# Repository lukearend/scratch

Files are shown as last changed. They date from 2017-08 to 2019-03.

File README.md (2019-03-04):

# scratch
_an open-source, autonomously-balancing mobile robot built from scratch_

See it in action [here](https://youtu.be/LrDqXtu8--8)!

## Overview

*scratch* is a self-balancing mobile robotics platform. The robot balances itself on two wheels using IMU sensors and a feedback loop with its motors. It drives using commands dictated from the user via a Sony DualShock 3 gamepad controller. Its balancing functions are handled by an Arduino Mega microcontroller, and its higher-level driving instructions and operations are handled by an on-board Raspberry Pi communicating with the Arduino. The goal of the project is to implement hierarchical control structure and explore the development of complex behavior in a partially autonomous mobile robotics system.

## How it works

### Goal of the self-balancing robot

The task at hand is to create a mobile robot which balances itself on two wheels. This is an implementation of the *inverted pendulum*, a classical problem in dynamics and control theory. The premise is simple: there is a pendulum which has its center of mass above its pivot point. This is an unstable equilibrium point, so in practice it will fall over due to noise in the environment. The goal is to move the pivot point horizontally in such a way that the weight remains upright. Naturally, this model and its variants are also important in the field of robotics and have seen several applications in recent years.

In the case of the self-balancing robot, the task is to drive the two wheels such that the agent maintains an upright, balanced posture. In theory, the problem is fairly straightforward. The agent must first acquire some knowledge of its current position in respect to its desired position. Next, it must calculate the actions needed to achieve its desired position. Finally, it needs to adjust its motor outputs accordingly in order to carry out these actions despite various affecting factors in the environment. This is carried out via a *closed-loop control system*, where actual sensory feedback is integrated with the desired state of the system in order to adjust the system toward its desired state.

In practice a solution is somewhat complicated. The real world poses a suite of complicating factors including sensor noise, computation time, and mechanical slippage. The implications of some of these factors are considered in the section below, where a practical solution to the self-balancing robot is briefly explained.

### Using accelerometer and gyroscope for angle estimate

It is essential that the agent has an awareness of its own position. In the case of the self-balancing robot, this means that the agent must know the angle of its body with respect to vertical at any given point.

To this end, two sensors are applied - the accelerometer and the gyroscope. The accelerometer measures the component of acceleration being experienced along any of the three axes at any given time. When the accelerometer is in a steady state, the primary acceleration experienced is that due to gravity. This essentially allows the accelerometer to tell which way is "down." In our case, the x and z components of the accelerometer are given to be in the plane of the robot as it tips forward and backwards. Thus, given both of these sensor readings, we can use inverse tangent trigonometry to calculate an angle estimate of the body from the accelerometer.

The gyroscope gives relatively low-noise readings, but accumulates bias over time; the accelerometer is very noisy but unbiased. The two sensors are integrated via a Kalman filter to provide a state estimate.

### Lowest level PID loop for motors
A very low-level short-time scale PID controller for each wheel adjusts the raw voltage supplied to the motor in order to achieve a target wheel speed.

### Middle level balancing PID loop
A mid-level PID controller adjusts the motor speed to supply to the low-level PID controller in order to orient the body to a particular target angle.

### Highest level driving PID loop, driving control and filtering
A high-level, longer-time scale PID controller adjusts the target angle to shoot for in order to achieve a target velocity.

The target velocity is given by the user via Playstation controller, and this signal can also be used to bias the robot toward balancing in one location.

### Peripherals such as proximity sensors (with filters) and servo motor neck
The robot is outfitted with a number of proximity sensors which could be used in the future for autonomous navigation. It also has a servo motor neck which points in the direction it is driving. This could be outfitted with a Raspberry Pi camera to do something like optic flow analysis for visual feedback or simple facial recognition using a lightweight convolutional neural network.

### Serial communication
The Arduino and Raspberry PI communicate asynochronously over serial. The Arduino control loop operates on a much faster timestep than the Raspberry Pi, so the Arduino receives a driving command every few loops. The Raspberry Pi waits, every loop, to hear back from the Arduino.

### Raspberry Pi connecting to controller using sixad and pairing with sixpair
The Raspberry Pi must be paired with the Playstation controller using sixad and pairing with sixpair. See [this blog](http://booting-rpi.blogspot.com/2012/08/dualshock-3-and-raspberry-pi.html) for a walkthrough.

## Instructions

### Starting up from completely powered down

#### Visual assessment

1. Visually assess the robot and its connections. Are the batteries charged? Are both battery packs plugged in properly (including the Turnigy lithium-polymer battery being plugged into the low voltage alarm)? Is the serial communication line between the Raspberry Pi and the Arduino intact? Are the servo motors hooked up properly? Are all the screw terminals holding securely? Having any wires become unseated from the protoboards? Are there any loose or fraying wires?

#### Launching the Raspberry Pi

2. Switch on the Raspberry Pi power bank. This can be done by pressing the power button found on the left, outer-facing side of the robot.

3. Gain access to the Raspberry Pi. The Raspberry Pi is running headlessly (which means it is not connected to any monitor, keyboard, mouse, etc.), so it must be controlled somehow. This can be done by hooking up an HDMI monitor and USB keyboard/mouse, or by accessing its command line through a remote secure shell server (enter `ssh pi@192.168.194.240` (or the Pi’s IP address) or `mosh pi@192.168.194.240` (if using the mosh client) into a terminal session connected over the same network, and enter the password, raspberry, when prompted, to connect). *(See appendix 3 for list of useful Linux shell commands).*

4. Launch the script. From the Raspberry Pi shell, enter the command `sudo python3 Programming/Python/Programs/flexibot.py` to launch the program which connects to the Sony DualShock 3 gamepad controller and operates the balancing robot.

5. The program will go through its initialization process. Follow the printed prompts to connect to the controller via Bluetooth. It may take several tries to get the Raspberry Pi to recognize the controller. *If this step is repeatedly unsuccessful, see appendix 4 for troubleshooting).*

6. Once the controller is connected, the Raspberry Pi will open its serial port and begin its communications with the Arduino.

7. At this point, the Raspberry Pi no longer needs to be controlled directly by the user. The monitor, keyboard, and/or mouse can be unplugged or the ssh or mosh session can be terminated. The Pi is now up and ready to go!

#### Launching the Arduino

8. Hold the robot in a straight upright position. This will help it get started off on the right foot, so to speak.

9. Throw the metal toggle switch on the front of the robot from `OFF` to `ON`.

10. The robot will calibrate and initialize itself, which should only take a second or so. The robot will then begin to balance on its own. *(If it does not spring into action at this point, see appendix 4 for troubleshooting).*

11. The system is now entirely operational.

### Operation instructions

#### Using the controller

Now that the robot is up and running, it can be operated by the user with the Sony DualShock 3 gamepad controller:

<table>
  <tr>
    <td>Left joystick left/right (mode 1)</td>
    <td>Turn left/right</td>
  </tr>
  <tr>
    <td>Right joystick up/down (mode 1)</td>
    <td>Drive forwards/backwards</td>
  </tr>
  <tr>
    <td>Left joystick up/down (mode 2)</td>
    <td>Left wheel forwards/backwards</td>
  </tr>
  <tr>
    <td>Right joystick up/down (mode 2)</td>
    <td>Right wheel forwards/backwards</td>
  </tr>
  <tr>
    <td>Left bumper</td>
    <td>Toggle between mode 1 and mode 2</td>
  </tr>
  <tr>
    <td>Right bumper</td>
    <td>Invert controls (aircraft style)</td>
  </tr>
  <tr>
    <td>D-pad up/down</td>
    <td>Increase/decrease speed multiplier by .25 m/s (min 0, default .5, max 1)</td>
  </tr>
  <tr>
    <td>D-pad right/left (!)</td>
    <td>Increase/decrease drive smoothing factor by .1 (min 0, default 1, max 1)</td>
  </tr>
  <tr>
    <td>Start (!)</td>
    <td>Launch/terminate autonomous mode</td>
  </tr>
  <tr>
    <td>Select (!)</td>
    <td>Terminate script</td>
  </tr>
</table>

The controls marked with the *(!)* sign are advanced controls. These should be operated with discretion, by the experienced user:

* It is recommended that maximum drive smoothing is used all the time, for the most stable and safe driving.

* Autonomous mode is highly experimental and subject to potentially destructive failures. It is worth mentioning that any movement of the joysticks at all during autonomous mode will manually override, terminating autonomous mode and giving control back to the user instantly.

* Terminating the script will require regaining access to the Raspberry Pi if the user wishes to relaunch the program.

Finally, pressing down all four buttons (triangle, circle, cross, and square) at the same time momentarily will reboot the Raspberry Pi (note that this does not relaunch the script). Holding these down for 3 seconds will cause the Raspberry Pi to shut down and remain powered off.

#### Driving tips

* When in doubt, go slow. There is generally more stability at slower speeds, and less stability at high speeds.

* Be very cautious when negotiating rough or uneven terrain. This is especially true where there are small gaps or elevated lips on the floor changing from one type of surface to another. If negotiated improperly, these can easily cause the robot to tip over violently. It is best to attempt to drive over these slowly and evenly. It is essential to cross at a 45 degree angle rather than head on so that the obstacle is handled one wheel at a time.

* The robot should be able to handle disturbances such as pushes or kicks to the top fairly well, but there is a limit. Pushing the robot’s wheels or holding them in place will likely cause it to fall over. The mobility of the wheels is the only mechanism by which it is able to balance itself.

* Do not pick up the robot while it is balancing. This disrupts the feedback loop in the robot’s control structure.

* Do not drive the robot into walls, or obstacles that will not allow its wheels to rotate.

* Do not operate on wet, slippery, sandy, or fiery surfaces.

### Powering down

The Arduino and Raspberry Pi have been designed to be capable of operating independently of one another. In other words, the Arduino can be switched on and off (for instance to drive the robot, pick it up and carry it for a while, drive it again) while the Raspberry Pi script is still running and staying connected to the controller. Likewise, the Arduino can operate independently of the Raspberry Pi, in which case the robot will simply balance in place devoid of driving instructions. The two should be able to switch on and off independently of one another.

When the user wishes to completely shut down the system, the following steps should be followed:

1. Switch off the Arduino. Make sure that it is held or properly supported so that it does not fall over.

2. Shut down the Raspberry Pi. This can be done by holding down all four buttons on the controller (triangle, circle, cross, and square) at the same time for three seconds. Otherwise, (such as if the controller has become disconnected, or the program was terminated), it can be done by plugging in a keyboard (or accessing via a remote shell server client) and issuing the shell command `sudo shutdown -h now`. This tells the Raspberry Pi to shut down immediately, and stay powered down (this is called a system halt). The yellow LED activity light on the Raspberry Pi will blink 10 times when it has fully shut down.

* *Important note:** It is absolutely imperative that the Raspberry Pi is properly shut down before its power supply is removed! Improper shutdown or simply switching off its power supply/pulling the plug can corrupt its filesystem, with the possibility of irreparably damaging the SD card and losing everything.

3. It is now safe to switch off the Raspberry Pi’s power bank. Hold the power button on the left outward-facing side of the robot for approximately one second until the power bank’s blue LED bars stop glowing.

4. The system is now entirely shut down.

### Battery management and storage

One crucial element to the long-term use and operation of the robot is proper management of the batteries powering the various devices making up the system.

#### Sony DualShock 3 gamepad controller battery

The controller operates wirelessly, so it must be recharged on occasion. Typically, a full charge will last for hours of use and takes only about 20-30 minutes. To charge, simply use a USB 2.0 A-male to mini-B cable to plug the controller into the Raspberry Pi when it is powered on. Note: the controller can be charged by plugging into some other devices, but this will cause it to become unpaired with the Raspberry Pi. It will have to be physically re-paired again with the Raspberry Pi after charging on another device.

#### Raspberry Pi power bank

Make sure that the Raspberry Pi is properly shut down before turning off the power bank and removing the USB power connection between the bank and the Raspberry Pi. The power bank can be recharged by plugging into a USB port or USB wall adapter with a USB 2.0 A-male to micro-B cable. The bank does not support through-charging, so it cannot be both charged and used to power the Raspberry Pi at the same time. The blinking blue LED bars on the side of the bank indicate its level while charging; when all the bars are on and no longer blinking, the bank is full.

#### Turnigy lithium-polymer battery

First of all, lithium-polymer batteries are volatile and highly dangerous if used improperly. It is strongly recommended that the user educate themselves on proper care, use, and storage of these batteries before operating the robot in any way.

The low voltage alarm will indicate when the battery needs to be recharged. Do not continue to operate the robot once the alarm has indicated that the cells are reaching low voltages, or else the battery may be irreparably damaged. 

To recharge the battery, the user should first completely shut down the robot. Then the battery can be carefully unplugged from the robot and removed from the chassis.  The battery should be charged using a proper lithium-polymer balance charger. Lithium-polymer batteries should never be charged unsupervised because of the risk of fire or explosion. Once the battery is charged, it can be once again carefully plugged back into the robot. Remember to plug it into the low voltage alarm as well, ensuring that it is connected with the proper polarity.

#### Storage

There are a few things to consider when storing the robot inactively for extended periods of time. 

First of all, the Raspberry Pi should be properly shut down and the Raspberry Pi power bank should be completely turned off.

Next, the battery should be unplugged from the low voltage alarm. If it remains plugged in, the alarm (which has several LEDs) will continue to sap power from the battery until it is completely dead. If a lithium-polymer battery is drained completely, it becomes irreparably damaged and is effectively rendered worthless. It is thus essential that the battery does not remain plugged into the low voltage alarm if it is not being used in the near future.

Furthermore, lithium-polymer batteries should not be stored for long periods of time at full charge or at low charge, or else the health of the battery will be adversely affected. Thus, the battery must be stored at a partial charge. This can be done by choosing the "STORAGE" setting on the balance charger, which will bring the cells to a proper voltage for safe and healthy long-term storage.

## Current known issues

*Serial communications breakdown may occur between the Arduino and the Raspberry Pi.* They are communicating at very high baud rates with very rapid control loops.

*The WiFi module on the Raspberry Pi sometimes does not work properly, and the Raspberry Pi can have issues connecting to the internet even with a wired internet connection.* This may be due to the Bethel ITS department’s current work on restructuring the network.

*The robot may struggle to balance on rough terrain or when encountering large disturbances.* Continuing work is being done on optimizing the balancing control algorithms.

*The servo motor head will sometimes become unresponsive while the rest of the robot continues to work properly.* This rare issue is likely caused by some sort of communication disruption between the Arduino and the ServoShield.

*Autonomous mode is still in the earliest stages of development.* The robot does not yet demonstrate advanced or even particularly successful autonomous behavior over extended periods of time.

## Future improvements

### Hardware

A small LCD touch screen will be mounted to the servo neck of the robot, as well as a PiCamera to be operated by the Raspberry Pi script. 3D print designs for these mounting cases have already been designed. The screen could be used to operate the Raspberry Pi easily, or display some type of robotic face or video stream. The camera could be used to capture images and video and save them to the Raspberry Pi’s filesystem. It also opens up the possibility for types of object recognition or machine vision to be incorporated in the future.

### Software

Now that a solid hardware robotics platform has been developed for the most part, the main future developments will be on the software side. The goal is to pursue deeper levels of autonomy in the form of hierarchical control structure, developing more advanced behaviors and combinations of reflex arcs. Measures may be taken to model functions of the human central nervous system in developing an efficient and effective control structure. Hopefully this system can be used as a platform to study real-world implementations of reinforcement learning, statistical learning, pattern recognition, localization and mapping, and other types of machine learning and artificial intelligence.

## Parts list

### Frame/Chassis

* M3 frame bolt *(numerous)*

* M3 nut *(numerous)*

* aluminum M3 L-bracket connector piece *(numerous)*

* aluminum M3 45-degree connector piece *(numerous)*

* aluminum M3 right angle connector piece *(numerous)*

* 4.0 cm aluminum frame piece *(x4)*

* 6.0 cm aluminum frame piece *(x5)*

* 10.0 cm aluminum frame piece *(x4)*

* 15.0 cm aluminum frame piece *(x6)*

* 20.0 cm aluminum frame piece *(x2)*

* [Actobotics 1.50" aluminum channel](https://www.sparkfun.com/products/12383)

  -fits perfectly around Turnigy lipo battery to hold it in using friction

* bottom chassis plate (with mounting holes for motors)

* neck chassis plate (with mounting holes for servo motor neck)

* 3M double-sided foam adhesive tape

* foam padding

* toggling power switch for Arduino power supply

* mounting board for Raspberry Pi (Sketchup files included)

* mounting board for Arduino

* mounting board for power regulator

* 4-40 standoff bolt (plastic) *(numerous)*

* 4-40 nut (plastic) *(numerous)*

* 4-40 washer (plastic) *(numerous)*

### Power supply

* [Turnigy 2200 mAh 3s 20C lithium-polymer battery pack](http://www.google.com/url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)

  -power supply for Arduino, its peripherals, DC motors and all lower-level sensors

* [AmazonBasics 5600 mAh portable power bank](http://www.amazon.com/AmazonBasics-Portable-Power-Micro-Cable/dp/B00LRK8HJ8)

  -power supply for Raspberry Pi and its peripherals

* [HobbyKing lipoly low voltage alarm](http://www.hobbyking.com/hobbyking/store/__18987__On_Board_Lipoly_Low_Voltage_Alarm_2s_4s_.html)

  -connected to lipo battery, alerts user when battery reaches low voltages

* [Polulu step-down voltage regulator D15V70F5S3](https://www.pololu.com/product/2111)

  -takes 11.1V from lipo battery and drops it to 5V to power Arduino and its sensors

### Arduino

* Arduino Mega 2560

  -the central microprocessing unit of the balancing sensors and control structure

* [Sparkfun MegaShield kit](https://www.sparkfun.com/products/9346)

  -prototyping shield for Arduino Mega

* [Sparkfun 3.3-5V bi-direction logic level converter](https://www.sparkfun.com/products/12009)

  -for interfacing Arduino serial communication (operating at 5V) with Raspberry Pi GPIO serial communication (operating at 3.3V)

* [Mini modular breadboard](https://www.sparkfun.com/products/12043) *(x2)*

  -adhesively attached to MegaShield for prototyping on the Mega

### DC motor control

* [Polulu dual MC33926 motor drive shield for Arduino](https://www.pololu.com/product/2503)

  -contains H-bridge circuitry to operate the DC motors to provide balancing functions

  -capable of operating at relatively high currents without heating up significantly

  -no heatsink needed

* Brushed DC motor with optical encoder *(x2)*

* [BaneBots 4 7/8 robot wheel](http://banebots.com/pc/WHB-WS-498/T80P-494BO-U3) *(x2)*

### Sensors

* [Sparkfun 9DOF LSM9DS0 IMU breakout](https://www.sparkfun.com/products/12636)

  -combined accelerometer/gyroscope/magnetometer sensor used for calculating an estimated angle of the robot, configured to communicate with Arduino via I2C protocol

  -*important:* operates at 3.3V

* [Sparkfun 3.3-5V bi-direction logic level converter](https://www.sparkfun.com/products/12009)

  -for interfacing Arduino I2C (operating at 5V) with LSM9DS0 I2C (operating at 3.3V)

* [Sharp GP2Y0A41SK0F short range infrared proximity sensor](https://www.sparkfun.com/products/12728) *(x4)*

  -two placed on front of robot facing forwards, two placed on back of robot facing backwards

  -used to help robot detect objects in autonomous exploration mode

* [Infrared sensor jumper wire](https://www.sparkfun.com/products/8733) *(x4)*

* [Mini modular breadboard](https://www.sparkfun.com/products/12043) *(x2)*

  -prototyping space where IMU sensor and its level shifter are wired

  -adhesively attached to back of battery mount, centered directly on axis with the wheelbase between DC motors

### Servo motor control

* [Renbotics ServoShield V2.0](http://www.seeedstudio.com/depot/Renbotics-ServoShield-V20-p-1299.html)

  -configured to communicate with Arduino via I2C in order to control up to 16 servos

  -*important:* the printed labels on the hardware channels 1-16 actually correspond to software channels 0-15; this discrepancy is handled in the Arduino program

* Servo motor *(x2)*

  -these servos provide 2 degrees of freedom for the neck: tilting forwards to backwards, and swiveling left to right

* Servo neck mounting pieces

### Raspberry Pi

* [Raspberry Pi 2 Model B](https://www.raspberrypi.org/products/raspberry-pi-2-model-b/)

  -the central high-level control unit taking wireless commands from controller via Bluetooth, and communicating them to Arduino via serial on GPIO pins

* [SanDisk Ultra 16GB microSDHC Class 10 memory card](http://www.bestbuy.com/site/sandisk-ultra-16gb-microsdhc-class-10-memory-card-black/4120107.p?id=1218457270079)

  -memory card housing filesystem for Raspberry Pi

* [Bluetoth 4.0 USB module](https://www.adafruit.com/products/1327)

  -provides Bluetooth capabilities for wireless communication with Sony DualShock 3 gamepad controller

* [Miniature WiFi (802.11b/g/n) module](https://www.adafruit.com/products/814)

  -provides WiFi capabilities to Raspberry Pi

  -especially useful for setting up remote SSH server (this [mosh mobile shell client](https://mosh.mit.edu/) is highly recommended) in order to remotely access Raspberry Pi command shell

  -also useful for setting up a remote VNC server (this [RealVNC remote VNC viewer](https://www.realvnc.com/) is highly recommended) in order to remotely access Raspberry Pi X-server desktop (the graphic user interface launched via "startx" command)

  -these features offer fantastically flexible operation of the Raspberry Pi; it can be controlled headlessly and wirelessly in the robot without the need to physically plug in a keyboard, mouse and monitor every time the user must execute a command, launch a script, properly shut down, etc.

* [Sony DualShock3 wireless gamepad controller](http://www.amazon.com/PlayStation-Dualshock-Wireless-Controller-Black-3/dp/B0015AARJI)

  -operated by user to drive the robot

  -communicates wirelessly with Raspberry Pi via Bluetooth

### Essential development tools and peripheral devices

* [IMAX B6 Lipro digital balance charger](http://www.amazon.com/Original-Lipro-Digital-Balance-Charger/dp/B006TT49O4)

  -used to charge/balance/store/discharge lithium-polymer batteries

* operating system running Arduino IDE environment

  -for developing and uploading Arduino source code to robot (written in Arduino C/C++)

* USB 2.0 A-male to B-male cable

  -for connecting Arduino to computer for uploading source code and serial monitoring

* HDMI-capable external monitor

  -for graphic display of Raspberry Pi during development

* USB keyboard

  -for keyboard control of Raspberry Pi during development

* USB mouse

  -for mouse control of Raspberry Pi during development

* USB 2.0 A-male to mini-B cable

  -for connecting Sony DualShock 3 gamepad controller to Raspberry Pi for charging and initial pairing process

* USB hub

  -allows several USB peripherals to connect to Raspberry Pi over one USB port

## Wiring connections and pinout

### Wiring diagram

*(See appendix 1.1.)*

### Pinout list

#### Arduino pinout

<table>
  <tr>
    <td>Analog input 0</td>
    <td>Motor L current sensing</td>
  </tr>
  <tr>
    <td>Analog input 1</td>
    <td>Motor R current sensing</td>
  </tr>
  <tr>
    <td>Analog input 4</td>
    <td>Front-left proximity sensor reading</td>
  </tr>
  <tr>
    <td>Analog input 5</td>
    <td>Front-right proximity sensor reading</td>
  </tr>
  <tr>
    <td>Analog input 6</td>
    <td>Back-left proximity sensor reading</td>
  </tr>
  <tr>
    <td>Analog input 7</td>
    <td>Back-right proximity sensor reading</td>
  </tr>
  <tr>
    <td>Digital 4</td>
    <td>Motor shield enable pin</td>
  </tr>
  <tr>
    <td>Digital 7</td>
    <td>Motor L direction pin</td>
  </tr>
  <tr>
    <td>Digital 8</td>
    <td>Motor R direction pin</td>
  </tr>
  <tr>
    <td>Digital 9</td>
    <td>Motor L pulse width modulation pin</td>
  </tr>
  <tr>
    <td>Digital 10</td>
    <td>Motor R pulse width modulation pin</td>
  </tr>
  <tr>
    <td>Digital 12</td>
    <td>Motor fault flag pin</td>
  </tr>
  <tr>
    <td>Digital 14 (Tx3)</td>
    <td>Serial communication with Raspberry Pi (Tx)</td>
  </tr>
  <tr>
    <td>Digital 15 (Rx3)</td>
    <td>Serial communication with Raspberry Pi (Rx)</td>
  </tr>
  <tr>
    <td>Digital 16</td>
    <td>Encoder L direction reading</td>
  </tr>
  <tr>
    <td>Digital 17</td>
    <td>Encoder R direction reading</td>
  </tr>
  <tr>
    <td>Digital 18 (interrupt 5)</td>
    <td>Encoder L interrupt pin</td>
  </tr>
  <tr>
    <td>Digital 19 (interrupt 4)</td>
    <td>Encoder R interrupt pin</td>
  </tr>
  <tr>
    <td>Digital 20 (SDA)</td>
    <td>Data signal for I2C communication</td>
  </tr>
  <tr>
    <td>Digital 21 (SCL)</td>
    <td>Clock signal for I2C communication</td>
  </tr>
</table>

#### ServoShield pinout

<table>
  <tr>
    <td>Hardware pin 15/Software pin 14</td>
    <td>Neck tilting servo motor</td>
  </tr>
  <tr>
    <td>Hardware pin 16/Software pin 15</td>
    <td>Neck swiveling servo motor</td>
  </tr>
</table>

#### Raspberry Pi pinout

<table>
  <tr>
    <td>Pin #6/GND</td>
    <td>Serial communication with Arduino (ground)</td>
  </tr>
  <tr>
    <td>Pin #8/GPIO14 (TxD0)</td>
    <td>Serial communication with Arduino (Tx)</td>
  </tr>
  <tr>
    <td>Pin #10/GPIO15 (RxD0)</td>
    <td>Serial communication with Arduino (Rx)</td>
  </tr>
</table>

### Device connection diagram

*(See appendix 1.2.)*

## Appendices

### 1.1 Wiring diagram

This diagram shows the electrical circuit connections of the entire system.

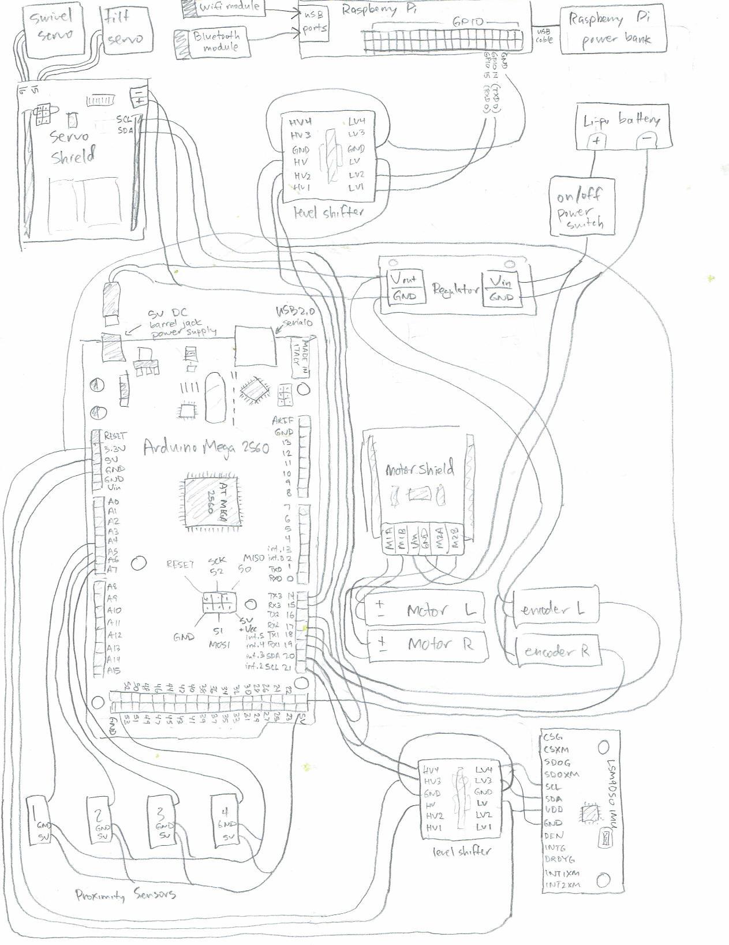
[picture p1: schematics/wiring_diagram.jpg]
wiring diagram


### 1.2 Device connection diagram

This diagram shows the overall connections between the various devices in the system. The hope is to give a general overview of which components are connected to each other, and how they are working together.

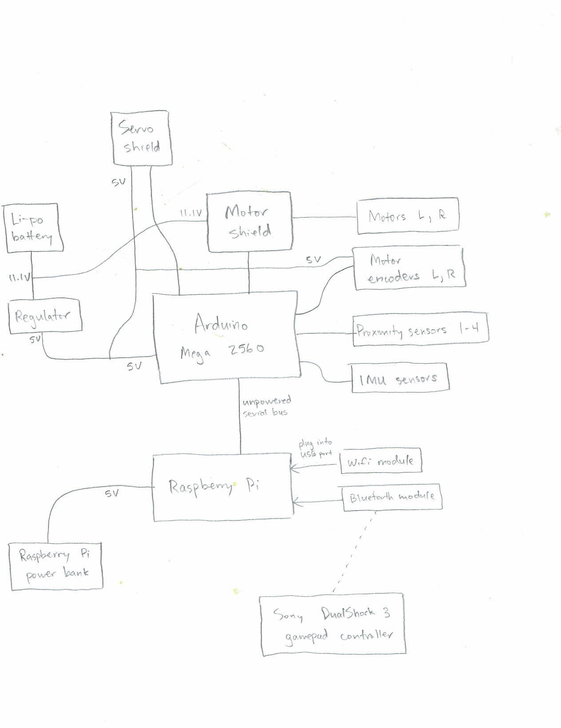
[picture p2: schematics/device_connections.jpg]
device connections


### 2.1 Hierarchical PID structure

This diagram shows the hierarchical nature of the primary PID controllers used in the system--a technique known as cascading PID control. The design of this system is modeled after the human central nervous system, where the brain influences the activity of the spinal cord to command voluntary movements. This is done through a hierarchy of control levels: *strategy* (represented by the association areas of neocortex and basal ganglia of the forebrain), *tactics* (represented by the motor cortex and cerebellum), and *execution* (represented by the brain stem and spinal cord).

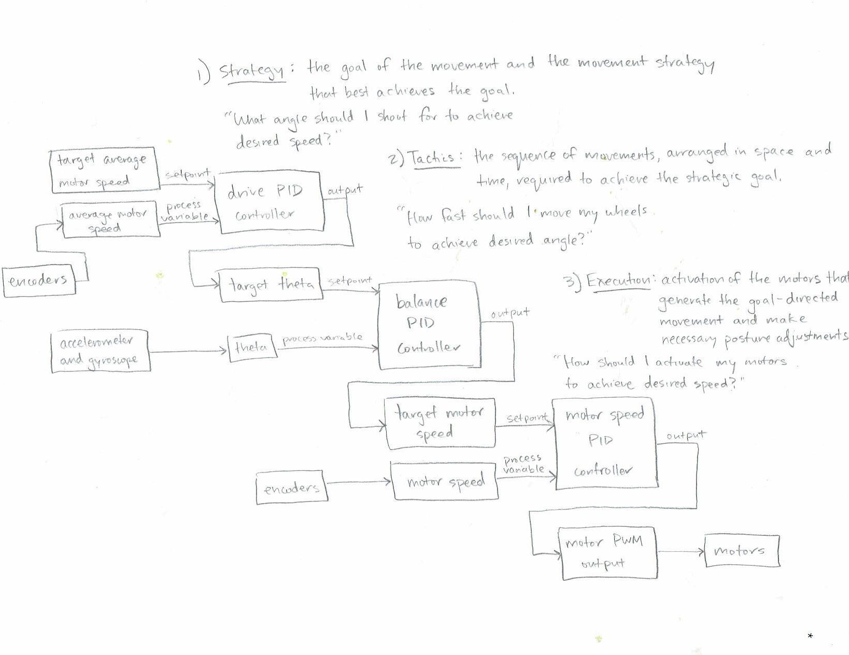
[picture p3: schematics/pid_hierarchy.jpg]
PID hierarchy


### 2.2 Control process block diagram

This diagram shows the flow of all control process occurring simultaneously in the robot.

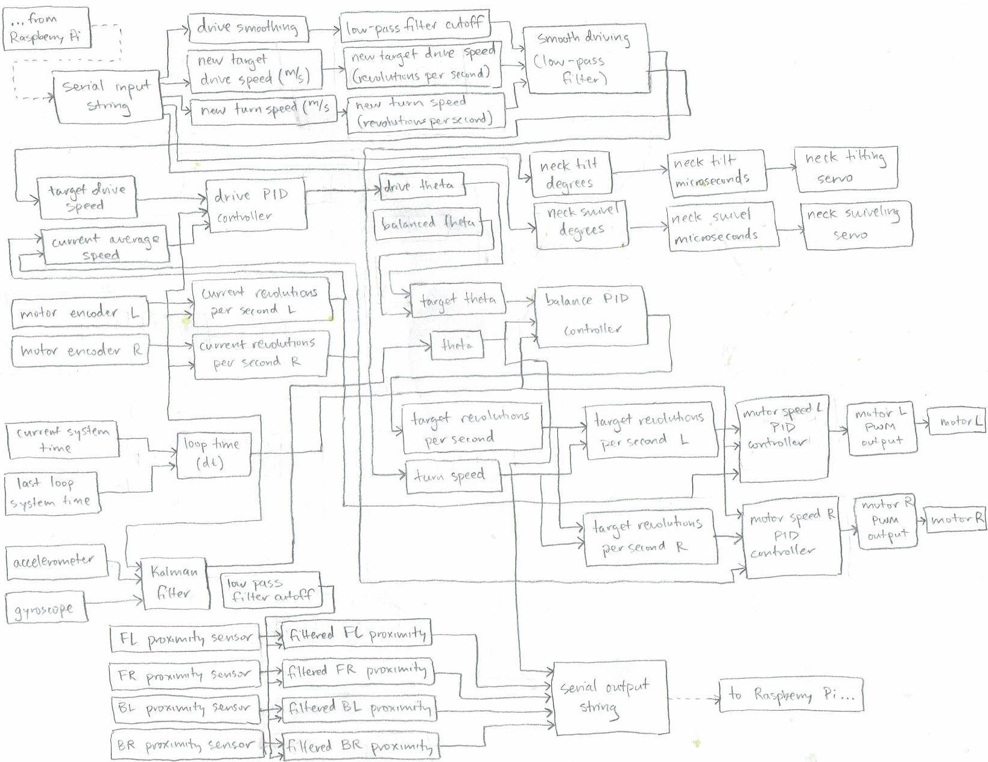
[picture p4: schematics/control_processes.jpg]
control processes


### 3. Useful Linux shell commands

`startx`: used to launch the graphic user interface (starts the X server which is the desktop)

`cd`: ‘call directory,’ navigates to the home directory

`cd ..`: navigates to the parent directory (up one folder)

`ls`: ‘library show,’ shows the contents of the current directory

`rm`: ‘remove,’ used to remove a file or directory

`sudo`: ‘superuser do,’ a powerful prefix that carries out any following command with superuser privileges (used when a command is being denied due to lack of permissions)

`sudo apt-get update`: connects to the internet and automatically downloads the latest updates for the distribution, should be run periodically and before major installments

`sudo service bluetooth status`: returns the current status of Bluetooth

`hciconfig`: displays useful information regarding Bluetooth functionality

`sudo ./sixpair`: runs an executable file pairing the Sony DualShock 3 gamepad controller with the Raspberry Pi (essentially performs a handshake with the controller)

`ifconfig`: displays useful information regarding network connection and various network devices such as ethernet and WiFi chips; can be used to find out current IP address

`sudo nano /etc/network/interfaces`: allows user to access and edit a text file containing important network configuration options; this is the file that must be used to set up a static IP address

`sudo reboot`: immediately reboots the Raspberry Pi

`sudo shutdown -h now`: immediately shuts down the Raspberry Pi and enters system halt mode where the filesystem is unmounted and the Raspberry Pi will stay powered down; it is then safe to unplug power supply

### 4. Troubleshooting

#### Raspberry Pi issues

*The Raspberry Pi boots up to a black screen.*

Check that the Raspberry Pi power bank is fully charged (all four blue LED bars are lit). Sometimes the Raspberry Pi needs to be operating on a fully charged battery to supply the power needed to launch the graphic user interface. Once the Pi is up and running, however, the power bank can generally run down without issue.

*The Linux shell is giving the error message *command not recognized* (or some similar variant).*

Check that the command is typed out exactly properly, letter for letter. Make sure that the user is currently in the correct folder, if attempting to carry out a particular command or access a particular file. See appendix for a list of useful Linux shell commands.

*The Python script repeatedly fails to connect to the Sony DualShock 3 gamepad controller.*

This could happen for a variety of reasons:

-Check that the Sony DualShock 3 gamepad controller is charged and working. The four red LED lights on the front should flash on and off when the PlayStation button is pressed.

-Try powering the controller off and back on again. Hold down the PlayStation button for approximately 10 seconds to shut off the controller, then try connecting again.

-Make sure that the Bluetooth chip is working properly. Enter the shell command sudo service bluetooth status and the response should be bluetooth is enabled. if Bluetooth is working correctly.

-If these are not the issue, the controller may need to be physically re-paired with the Raspberry Pi. This is the case if the controller has been plugged into another computer for charging, or has been used on another device. Follow these instructions in the Linux shell:

Enter the command cd in order to navigate to the home directory.

Enter the command cd Programming to navigate to the directory called "Programming". This directory contains an executable file called “sixpair”.

Plug the controller into the Raspberry Pi using a USB 2.0 A-male to mini-B cable.

Run the command sudo ./sixpair in order to pair the two devices. If they have paired successfully, the output should look similar to this:

Current Bluetooth master: DE:AD:BE:EF:00:00

Setting master bd_addr to**: 00:1F:81:00:06:2**

Now that the devices have been paired, the controller can be unplugged from the Raspberry Pi.

Navigate back to the home directory with the command cd and execute the script sudo python3 Programming/Python/Programs/flexibot.py again in order to re-attempt connecting the controller wirelessly.

-If these measures are unsuccessful, try following the instructions found in [this guide](http://booting-rpi.blogspot.com/2012/08/dualshock-3-and-raspberry-pi.html).

*The robot is up and balancing, but the Sony DualShock 3 gamepad controller does nothing.*

This means that the Arduino is working properly in balancing the robot, but it is not receiving driving commands from the Raspberry Pi. This could be because the Raspberry Pi has stopped running its script, or the script is still running and the controller is not being detected by the Raspberry Pi. Try re-starting the script.

In any case, the Arduino is programmed to simply stop and balance in place in the absence of driving commands from the Raspberry Pi. *Informational note:* in qualitative experiments, the Bluetooth communication between the controller and the robot demonstrated an impressive range. It is likely that the robot would drive out of sight before its connection to the controller would be dropped.

#### Arduino issues

*When switching on the Arduino, the red power LED turns on but the robot does not start balancing.*

This issue is suspected to occur occasionally when the Arduino’s Serial3 buffer has been filled up by data streaming from the Raspberry Pi. This prevents the Arduino from going through its normal initialization process and launching its code, springing into action. Try switching off the Arduino, carefully unplugging the ribbon cable serial connection to the Raspberry Pi, and firmly plugging it back in again. Try switching on the Arduino again.

*The robot sort of balances, but it begins to drive itself in circles and falls over.*

This nasty issue occurs when the motor encoder on one of the wheels is not providing proper feedback. Try carefully observing the electrical activity on pins 16-19 with an oscilloscope while manually rotating the wheels to check if everything is working properly. The line in the Arduino source code responsible for driving the motors normally must be commented out in order to try this.

#### Hardware issues

*The robot is balancing somewhat well, but one of the wheels is a little bit jerky; almost as if it is lagging behind the other wheel.*

Switch off the robot and check that both wheels are tightened into the axle properly. If a wheel has become loose, it must be removed off and the axle must be tightened with a small hex key.

## Acknowledgments

Thanks to Profs. Nathan Lindquist and Adam Johnson at Bethel University for their mentorship and guidance throughout this project.

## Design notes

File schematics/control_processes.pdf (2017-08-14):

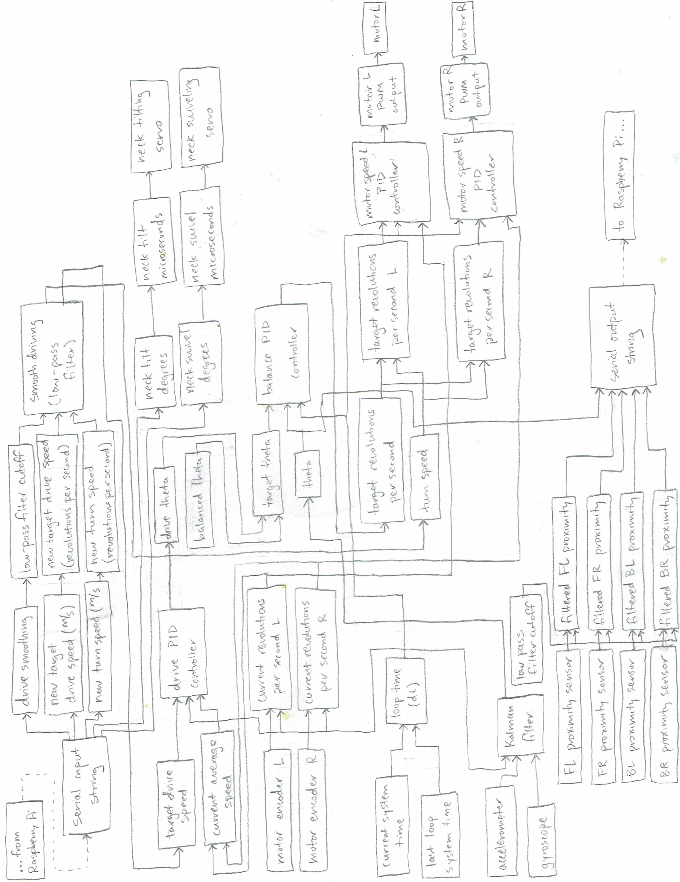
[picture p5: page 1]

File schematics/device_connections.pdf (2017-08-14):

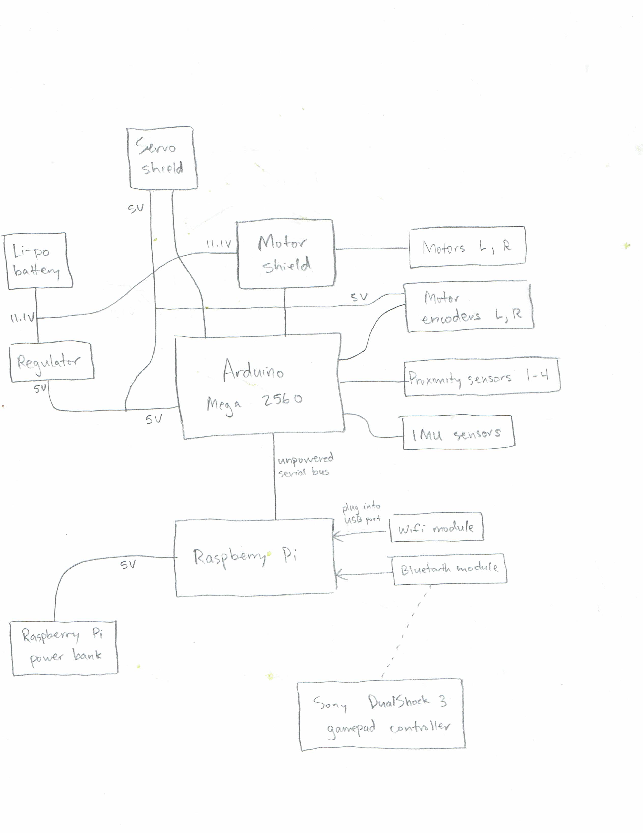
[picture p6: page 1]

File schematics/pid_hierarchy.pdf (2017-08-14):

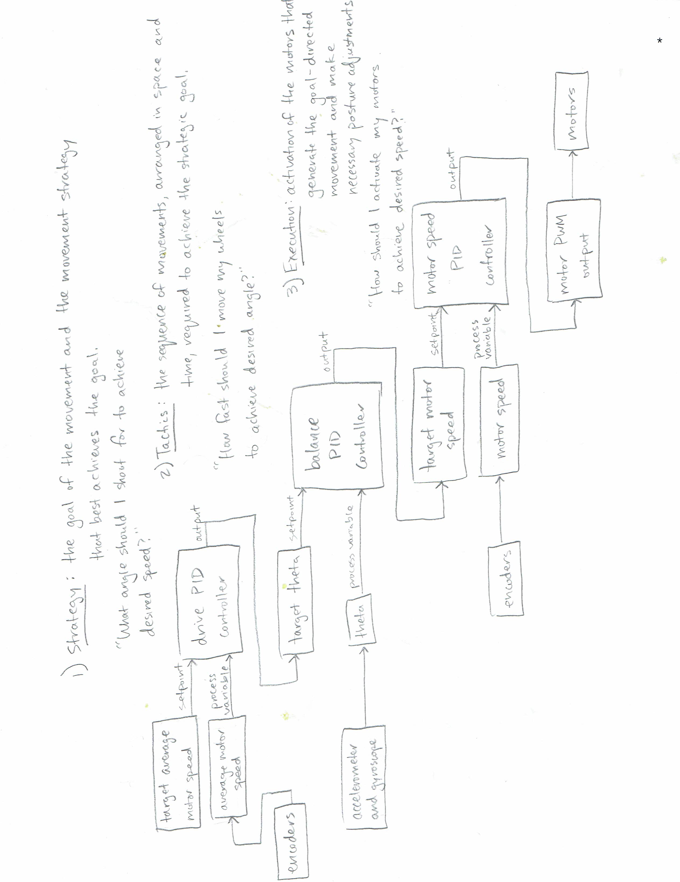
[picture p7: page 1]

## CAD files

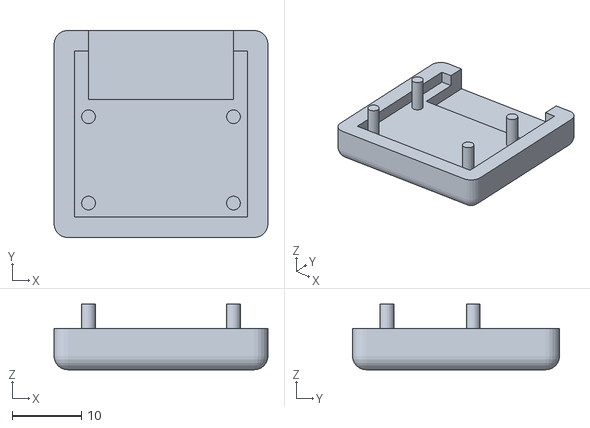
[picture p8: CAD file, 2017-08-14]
3d_prints/picamera_case/piCameraCaseBottom.stl
31.0 x 30.0 x 9.50

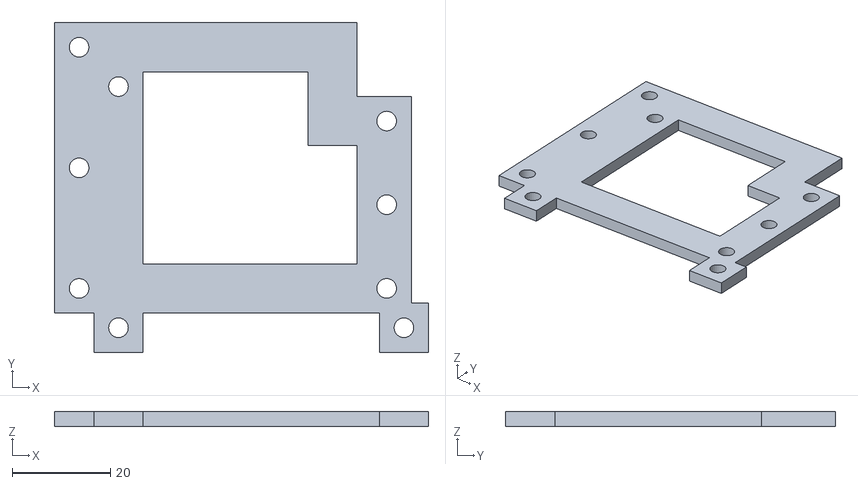
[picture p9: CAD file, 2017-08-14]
3d_prints/rpi_mount/raspberryPiMount.stl
76.0 x 67.0 x 3.00

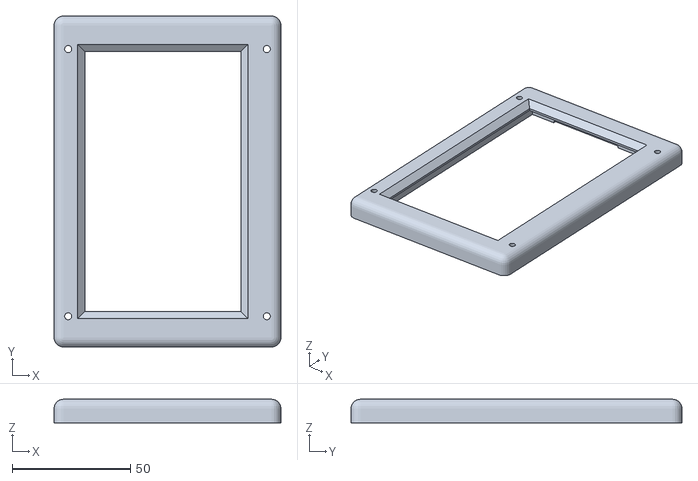
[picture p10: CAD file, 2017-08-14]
3d_prints/touchscreen_case/touchscreenCaseTop.stl
96.0 x 140.0 x 10.0

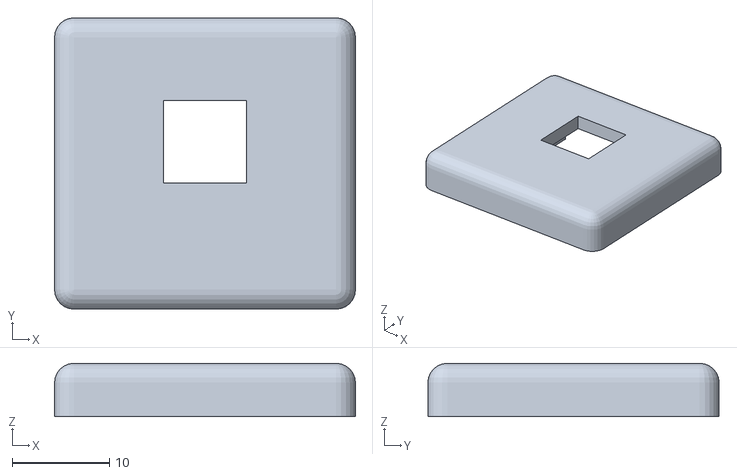
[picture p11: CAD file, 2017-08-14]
3d_prints/picamera_case/piCameraCaseTop.stl
31.0 x 30.0 x 5.50

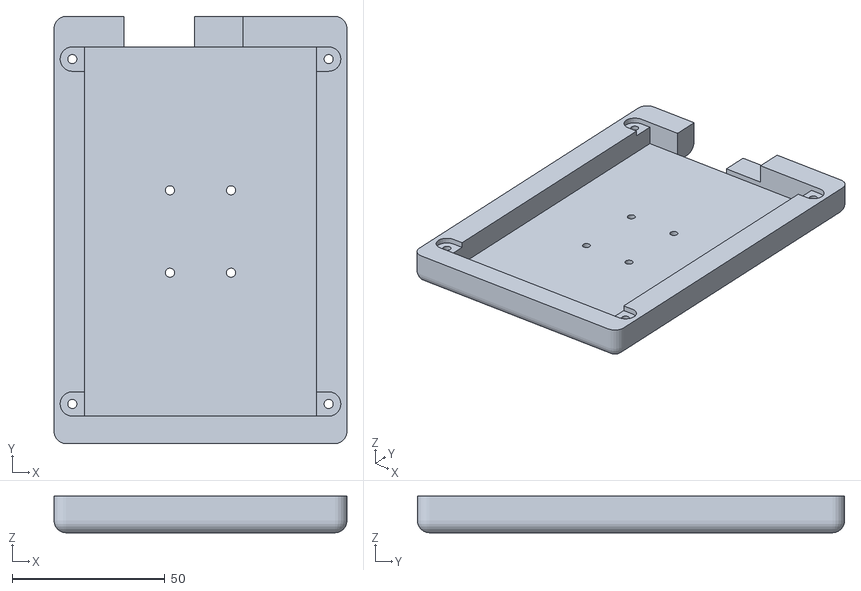
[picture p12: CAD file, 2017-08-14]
3d_prints/touchscreen_case/touchscreenCaseBottom.stl
96.0 x 140.0 x 12.0

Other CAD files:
3d_prints/picamera_case/piCameraCase.skp
3d_prints/rpi_mount/raspberryPiMount.skp
3d_prints/touchscreen_case/touchscreenCase.skp

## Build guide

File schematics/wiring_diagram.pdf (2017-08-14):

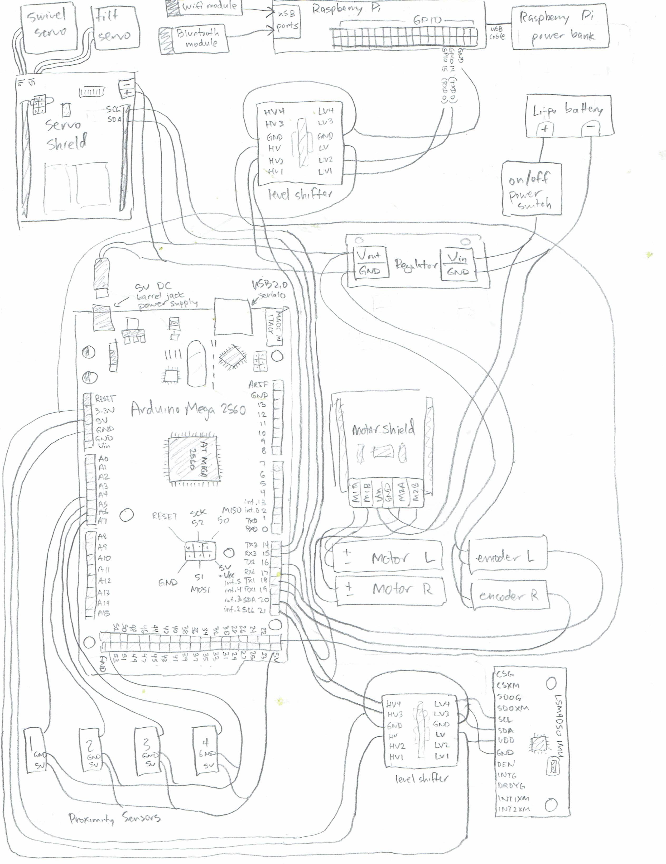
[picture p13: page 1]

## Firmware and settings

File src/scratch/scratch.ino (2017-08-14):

//////////////////////////////////////////////////////////////
//////////////////////////////////////////////////////////////
//////////////////////////////////////////////////////////////
//////////////////////////////////////////////////////////////
//////////                                          //////////
//////////                                          //////////
//////////                 SCRATCH                  //////////
//////////          for Arduino Mega 2560           //////////
//////////               Version 1.0                //////////
//////////                                          //////////
//////////                Luke Arend                //////////
//////////                Summer 2015               //////////
//////////        Bethel University NanoLab         //////////
//////////                                          //////////
//////////    Copyright © 2015 Bethel University    //////////
//////////           All rights reserved.           //////////
//////////                                          //////////
//////////                                          //////////
//////////////////////////////////////////////////////////////
//////////////////////////////////////////////////////////////
//////////////////////////////////////////////////////////////
//////////////////////////////////////////////////////////////




/*  PROJECT NOTES
 *  Enjoy!
 *  
 *  Hardware notes:
 *  -Wheel circumference is .388 m
 *  -Encoders will register 3000 counts per revolution
 *  -The left motor encoder sometimes has issues.
 *  -The left wheel sometimes physically becomes loose on the axle.
 *  -Make sure the motor shield is able to draw enough current--should not be an issue.
 *  -Arduino serial port 1 is open for communication with user via USB cable.
 *  -Arduino serial port 3 is connected via a 5v-3.3v level shifter to a Raspberry Pi.
 *  -The IMU sensors are read over I2C protocol.
 *  -The four infrared proximity sensors are read via an ADC over I2C protocol.
 *  -The angle positions for the servo motors in the neck correspond to microseconds in
 *  the PWM duty cycle. By experimentation, the following mapping was foundg:
 *    DEGREES <---->  MICROSECONDS
 *    TILT SERVO:
 *    0       <---->  1060
 *    45      <---->  1320
 *    90      <---->  1580
 *    135     <---->  1840
 *    <<180   <---->  1960
 *    SWIVEL SERVO:
 *    >>0     <---->  1000
 *    45      <---->  1220
 *    90      <---->  1500
 *    135     <---->  1780
 *    <<180   <---->  2000
 *  
 *  Software notes:
 *  -PID controllers are used throughout. I highly recommend the Ziegler-Nichols PID tuning method
 *  as a starting point.
 *  -I tend to err on the side of clarity at the expense of brevity. I often employ long or even
 *  descriptive function and variable names, or even ever-so-slightly suboptimal code for the sake
 *  of spelling out what is really going on.
 *  -There is heavy use of global variables. When programming for embedded microcontrollers this is 
 *  something of a necessary evil, and many of the pitfalls that normally accompany globals do not 
 *  apply. In this case, it often makes things simpler and allows more flexibility with functions. 
 *  The extensive use of global variables is a conscientious decision that I stand by.
 *  -I changed the Adafruit_ADS1015 library in order to optimize the proximity sensor reading speeds.
 *  Because of this, the pin mapping for the ADC converter is somewhat different because each is
 *  actually reading the sensor at the pin called before it. To read a physical pin, follow this mapping:
 *    read hardware pin 0 -> call software pin 0x01
 *    read hardware pin 1 -> call software pin 0x02
 *    read hardware pin 2 -> call software pin 0x03
 *    read hardware pin 3 -> call software pin 0x00
 *  -Due to this hangup, for the time being we are using analog read pins for the proximity sensors.
 */




//////// Library includes ////////
#include <math.h> // yay! we can do ALL the trigs
#include <SPI.h>  // included for SPI communications
#include <Wire.h> // included for I2C communications
#include <Adafruit_ADS1015.h> // library for using the ADS1015 12-bit ADC (optimized to be faster)
#include <SFE_LSM9DS0.h>  // library for using the LSM9DS0 9DOF gyro/accel/mag IMU
#include <ServoShield2.h>  // for neck servo motors



//////// Constant definitions ////////
//// Constants for motor encoders ////
#define ENCODER_L_BITMASK 2 // bit mask for a low level readng of pin 16
//^ ATmega2560 pin 13, PH1 ( TXD2 ), (port H, address B00000010)
#define ENCODER_R_BITMASK 1 // bit mask for a low level reading of pin 17
//^ ATmega2560 pin 12, PH0 ( RXD2 ), (port H, address B00000001)


//// Constants for driving control ////
#define RPS_TO_MPS .388 // constant conversion rate for revolutions per second to meters per second
#define MPS_TO_RPS 2.57732  // constant conversion rate for meters per second to revolutions per second


//// Tuning constants for drive PID controller ////
#define DRIVE_OUTPUT_GAIN 1 // output gain used to scale controller
#define DRIVE_P_GAIN 6.5  // P gain 6.5
#define DRIVE_I_GAIN 5  // I gain 7
#define DRIVE_D_GAIN .045 // D gain .045


//// Constants for IMU sensor ////
// I2C address constants for SFE_LSM9DS0 library //
#define LSM9DS0_XM_ADDR 0x1D // I2C address of accel/mag
#define LSM9DS0_G_ADDR  0x6B // I2C address of gyro

// Constants for scaling sensor readings //
#define RAD_TO_DEG 57.29578 // constant conversion rate for radians to degrees
#define DEG_TO_RAD 0.0174533  // constant conversion rate for degrees to radians
#define ACCEL_SCALE_X -1.09 // used to "zero out" accel readings at 1g
#define ACCEL_OFFSET_X 0
#define ACCEL_SCALE_Z -1.05
#define ACCEL_OFFSET_Z -.05


//// I2C address constant for ADC converter ////
#define ADS1015_ADDR 0x48


//// I2C address constant for servo shield ////
#define SERVO_SHIELD_ADDR 0x7F // can be changed with switch register on servo shield


//// Constants for Kalman filter ////
#define R_MEASUREMENT 0.03  // measurement noise variance (how much you distrust new measurements)
#define Q_ANGLE 0.001 // accelerometer variance (how much you distrust accelerometer readings)
#define Q_GYROBIAS 0.003  // gyro bias variance (how much you distrust gyro readings)
//^ these constants must be estimated or derived experimentally


//// Tuning constants for motor speed PID controller ////
#define SPEED_OUTPUT_GAIN 1 // output gain used to scale controller
#define SPEED_P_GAIN 180 // P gain 180
#define SPEED_I_GAIN 2000.15  // I gain 2000.15
#define SPEED_D_GAIN 1.57639  // D gain 1.57639


//// Tuning constants for balance PID controller
#define BALANCE_OUTPUT_GAIN -1  // output gain used to scale controller
#define BALANCE_P_GAIN 10.8  // P gain 10.8
#define BALANCE_I_GAIN 189.968  // I gain 189.968
#define BALANCE_D_GAIN .002  // D gain .002

#define DEFAULT_BALANCE_THETA 3 // the theta of the robot (with no adjustments) resulting in balance



//////// Class constructors ////////
//// Proximity sensors class ////
Adafruit_ADS1015 adc(ADS1015_ADDR); // class instance for ADS1015 called 'adc'


//// IMU class ////
LSM9DS0 imu(MODE_I2C, LSM9DS0_G_ADDR, LSM9DS0_XM_ADDR); // class instance for LSM9DS0 called 'imu'


//// Servo motor classes ////
ServoShield2 neck = ServoShield2(SERVO_SHIELD_ADDR, 50); // class instance for controlling neck servos
//^ sets servo update rate to 50 Hz mode



//////// Pin assignments ////////
//// Pin assignments for motor encoders ////
const byte encoderLpinA = 18;  // ATmega2560 pin 46, address PD3 (TXD1/INT3)
const byte encoderLpinB = 19;  // ATmega2560 pin 45, address PD2 (RXD1/INT2)
const byte encoderRpinA = 20;  // ATmega2560 pin 44, address PD1 (SDA/INT1)
const byte encoderRpinB = 21;  // ATmega2560 pin 43, address PD0 (SCL/INT0)


//// Pin assignments for infrared proximity sensors ////
/*const byte proxFLpin = 0x01; // front-left proximity sensor ADS1015 pin
const byte proxFRpin = 0x02; // front-right proximity sensor ADS1015 pin
const byte proxBLpin = 0x03; // back-left proximity sensor ADS1015 pin
const byte proxBRpin = 0x00; // back-right proximity sensor ADS1015 pin
//^ refer to project notes for why these are what they are*/

const byte proxFLpin = A4; // front-left proximity sensor ADS1015 pin
const byte proxFRpin = A5; // front-right proximity sensor ADS1015 pin
const byte proxBLpin = A6; // back-left proximity sensor ADS1015 pin
const byte proxBRpin = A7; // back-right proximity sensor ADS1015 pin


//// Pin assignments for motor driver  ////
const byte motorEnablePin = 4; // LOW = disabled, HIGH = enabled, toggling resets latched fault condition
const byte motorFaultPin = 12; // status flag indicator (LOW indicates fault)

const byte motorLpin = 7; // Polulu Dual MC33926 motor driver channel 1 direction input
const byte pwmLpin = 9;  // Polulu Dual MC33926 motor driver channel 1 speed input
const byte motorRpin = 8; // Polulu Dual MC33926 motor driver channel 2 direction input
const byte pwmRpin = 10; // Polulu Dual MC33926 motor driver channel 2 speed input

const byte motorLcurrentPin = A0;
const byte motorRcurrentPin = A1;


//// Pin assignments for servo neck (these pins are on ServoShield) ////
const byte neckTiltPin = 14;
const byte neckSwivelPin = 15;


//// Pin assignments for flexible actuators ////
const byte flex0driveApin = 23;
const byte flex0driveBpin = 25;
const byte flex0enablePin = 22;
const byte flex0currentPin = 62;  // A8
const byte flex1driveApin = 27;
const byte flex1driveBpin = 29;
const byte flex1enablePin = 24;
const byte flex1currentPin = 63;  // A9
const byte flex2driveApin = 31;
const byte flex2driveBpin = 33;
const byte flex2enablePin = 26;
const byte flex2currentPin = 64;  // A10
const byte flex3driveApin = 35;
const byte flex3driveBpin = 37;
const byte flex3enablePin = 28;
const byte flex3currentPin = 65;  // A11
const byte flex4driveApin = 39;
const byte flex4driveBpin = 41;
const byte flex4enablePin = 30;
const byte flex4currentPin = 66;  // A12
const byte flex5driveApin = 43;
const byte flex5driveBpin = 45;
const byte flex5enablePin = 32;
const byte flex5currentPin = 67;  // A13
const byte flex6driveApin = 47;
const byte flex6driveBpin = 49;
const byte flex6enablePin = 34;
const byte flex6currentPin = 68;  // A14
const byte flex7driveApin = 51;
const byte flex7driveBpin = 53;
const byte flex7enablePin = 36;
const byte flex7currentPin = 69;  // A15

const byte flex0num = 0; // gives pins 23, 25, 22, A8 (62)
const byte flex1num = 1; // gives pins 27, 29, 24, A9 (63)
const byte flex2num = 2; // gives pins 31, 33, 26, A10, (64)
const byte flex3num = 3; // gives pins 35, 37, 28, A11 (65)
const byte flex4num = 4; // gives pins 39, 41, 30, A12 (66)
const byte flex5num = 5; // gives pins 43, 45, 32, A13 (67)
const byte flex6num = 6; // gives pins 47, 49, 34, A14 (68)
const byte flex7num = 7; // gives pins 51, 53, 36, A15 (69)
//^ refers to the motor number, from which the pins can be derived as a linear function
//^ this saves from having to type out all the pin numbers when they follow an easy pattern



//////// Global variable declarations ////////
//// Global variables for loop timing ////
long int dt;  // main loop time step in microseconds
long unsigned int lastLoopTime; // system time of last main loop in microseconds


//// Global variables for serial communication ////
String inputString;


//// Global variables for motor encoders ////
volatile long int encoderL;  // long term encoder position storage, updated in interrupt
volatile long int encoderR;

long int lastEncoderL;  // used to store the value of encoder from last loop
long int lastEncoderR;

float rpsL; // measured motor speed in revolutions per second
float rpsR;

float avgSpeed; // average speed of both motors, low-pass filtered over time


//// Global variables for driving control ////
float driveSmoothing;  // smoothing LPF factor for ramping controls
float targetDriveSpeed;  // raw controller value of speed for robot to drive along
float turnSpeed; // raw controller value of turning for robot

float newTargetDriveSpeed; // new unfiltered command from controller, used in smoothing
float newTurnSpeed;
unsigned int serialCounter;  // counts how many loops have passed without any serial data


//// Global variables for drive PID controller ////
float driveErrorSum;  // sum of past errors
float driveLastError; // last error value used in driving PID controller


//// Global variables for proximity sensors ////
float proxFL;  // filtered proximity from front-left proximity sensor (in cm)
float proxFR;  // filtered proximity from front-right proximity sensor (in cm)
float proxBL;  // filtered proximity from back-left proximity sensor (in cm)
float proxBR;  // filtered proximity from back-right proximity sensor (in cm)


//// Global variables for Kalman filter ////
float theta;  // estimated actual angle of robot, the holy grail of the Kalman filter
float gyroBias; // drift in gyro reading
float P[2][2];  // error covariance matrix (how much you distrust the estimate of the state)
float S;  // innovation covariance (how much you distrust the innovation)
float K[2]; // Kalman gain matrix (how much you distrust the innovation)


//// Global variables for motor speed PID controller ////
float speedLErrorSum;  // sum of past errors (integral term)
float speedLLastError; // last error value used in motor speed PID controller
float speedRErrorSum;
float speedRLastError;


//// Global variables for balance PID controller ////
float balanceErrorSum;  // sum of past errors (integral term)
float balanceLastError; // last error value used in balance PID controller

float balanceTheta;  // the theta of the robot resulting in balance

float killTheta = 35; // the angle at which the robot gives up trying to balance and dies


//// Global variables for servo neck ////
float tiltDegrees;
float swivelDegrees;


//// Global variables for flexible actuators ////
//


//////// Main code ////////
//// Setup and initialization ////
void setup()
{
  // Initialize interrupt functions //
  attachInterrupt(5, readEncoderL, FALLING); // interrupt function 5 is hard-coded to pin 18
  attachInterrupt(4, readEncoderR, FALLING); // interrupt function 4 is hard-coded to pin 19
  
  // Initialize serial communications //
  Serial.begin(250000);
  Serial.setTimeout(5);

  Serial3.begin(115200);
  Serial.setTimeout(5);
  serial3Flush();

  // Initialize pin modes //
  pinMode(encoderLpinA, INPUT_PULLUP);  // the ATMega2560's internal pullup resistors are used
  pinMode(encoderLpinB, INPUT_PULLUP);  // this helps the motor encoders work more reliably
  pinMode(encoderRpinA, INPUT_PULLUP);
  pinMode(encoderRpinB, INPUT_PULLUP);

  pinMode(15, INPUT_PULLUP);  // Serial3 Rx pin is configured with internal pullup resistor

  pinMode(motorEnablePin, OUTPUT);
  pinMode(motorFaultPin, INPUT);
  pinMode(motorLpin, OUTPUT);
  pinMode(pwmLpin, OUTPUT);
  pinMode(motorRpin, OUTPUT);
  pinMode(pwmRpin, OUTPUT);

  pinMode(proxFLpin, INPUT);
  pinMode(proxFRpin, INPUT);
  pinMode(proxBLpin, INPUT);
  pinMode(proxBRpin, INPUT);

  pinMode(flex0driveApin, OUTPUT);
  pinMode(flex0driveBpin, OUTPUT);
  pinMode(flex0enablePin, OUTPUT);
  pinMode(flex0currentPin, INPUT);
  pinMode(flex1driveApin, OUTPUT);
  pinMode(flex1driveBpin, OUTPUT);
  pinMode(flex1enablePin, OUTPUT);
  pinMode(flex1currentPin, INPUT);
  pinMode(flex2driveApin, OUTPUT);
  pinMode(flex2driveBpin, OUTPUT);
  pinMode(flex2enablePin, OUTPUT);
  pinMode(flex2currentPin, INPUT);
  pinMode(flex3driveApin, OUTPUT);
  pinMode(flex3driveBpin, OUTPUT);
  pinMode(flex3enablePin, OUTPUT);
  pinMode(flex3currentPin, INPUT);
  pinMode(flex4driveApin, OUTPUT);
  pinMode(flex4driveBpin, OUTPUT);
  pinMode(flex4enablePin, OUTPUT);
  pinMode(flex4currentPin, INPUT);
  pinMode(flex5driveApin, OUTPUT);
  pinMode(flex5driveBpin, OUTPUT);
  pinMode(flex5enablePin, OUTPUT);
  pinMode(flex5currentPin, INPUT);
  pinMode(flex6driveApin, OUTPUT);
  pinMode(flex6driveBpin, OUTPUT);
  pinMode(flex6enablePin, OUTPUT);
  pinMode(flex6currentPin, INPUT);
  pinMode(flex7driveApin, OUTPUT);
  pinMode(flex7driveBpin, OUTPUT);
  pinMode(flex7enablePin, OUTPUT);
  pinMode(flex7currentPin, INPUT);
  
  // Initialize PWM duty cycle for pins 9 and 10 on ATMega2560 timer 2 (TCCR2B) //
  byte eraser = B000;
  TCCR2B &= eraser;
  //^ this operation erases the first three bits in TCCR2B (CS00, CS01, and CS02) to zero
  //^ these three bits hold the prescaling value for the timer counter
  byte prescaler = B001; // prescaler value of 1 is 31250 Hz
  TCCR2B |= prescaler;
  //^ this operation replaces the first three bits in TCCR2B with the new prescaling value
  //^ viola! motor pwm operates silently at 31.25 kHz, well above human hearing

  // Initialize motors to speed of zero and enable //
  digitalWrite(motorEnablePin, LOW);
  digitalWrite(pwmLpin, LOW);
  digitalWrite(pwmRpin, LOW);
  digitalWrite(motorLpin, LOW);
  digitalWrite(motorRpin, LOW);
  digitalWrite(motorEnablePin, HIGH);

  // Initialize servo neck //
  neck.start();
  neck.setbounds(neckTiltPin, 1060, 1960);
  neck.setbounds(neckSwivelPin, 1000, 2000);
  tiltDegrees = 90;
  swivelDegrees = 90;
  setNeck(tiltDegrees, swivelDegrees);

  // Initialize LSM9DS0 //
  imu.begin(imu.G_SCALE_245DPS, imu.A_SCALE_2G, imu.M_SCALE_2GS, imu.G_ODR_380_BW_100, imu.A_ODR_400, imu.M_ODR_100);
  //^ set gyro scale to 245 deg/sec, accel scale to 2g, mag scale to 2 gauss
  //^ set gyro data rate to 380 Hz, accel data rate to 400 Hz, mag data rate to 100 Hz

  /*// Initialize ADS1015 //
  adc.begin();
  TWBR = 0x02; // changes constant in Wire library to set I2C clock rate to 400kHz instead of 100kHz
  //^ also changed constant TWI_FREQ to 500000L in twi.h file of Wire.h library to speed it up*/
  
  // Initialize and calibrate Kalman filter //
  theta = DEFAULT_BALANCE_THETA; // initialize filter with estimate that robot started out in balanced position
  for(int i = 0; i < 500; i++)  // takes 500 readings to get actual starting theta
  {
    updatedt();
    
    float accelTheta = getAccelTheta(); // reading from accelerometer representing angle
    float gyroOmega = getGyroOmega(); // reading from gyroscope representing angular velocity

    kalmanFilter(accelTheta, gyroOmega);  // updates theta using complimentary filter
  }

  // Initialize last time and encoder values //
  lastLoopTime = micros();
  lastEncoderL = getEncoderL();
  lastEncoderR = getEncoderR();
}


//// Interrupt functions ////
void readEncoderL() // interrupt function which reads encoder from motor L
//^ triggered when pin 18 goes LOW
{
  if(PINH & ENCODER_L_BITMASK)  // if pin 16 is HIGH
  {
    encoderL++;
  }
  else  // if pin 16 is LOW
  {
    encoderL--;
  }
}

void readEncoderR() // interrupt function which reads encoder from motor R
//^ triggered when pin 19 goes LOW
{
  if(PINH & ENCODER_R_BITMASK)  // if pin 17 is HIGH
  {
    encoderR--;
  }
  else  // if pin 17 is LOW
  {
    encoderR++;
  }
}


//// Loop runtime function ////
void updatedt()  // calculates global variable dt and updates last loop time
{
  dt = micros() - lastLoopTime;
  lastLoopTime = micros();
}


//// Serial input functions ////
void serial3Flush() // flushes the receiving buffer for serial port 3
{
  while(Serial3.available())
  {
    Serial3.read();
  }
}
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
void loop()
{
  updatedt();

  serial3Check();
    
  updateRps();
  avgSpeed = .93*avgSpeed + .07*(rpsL + rpsR)/2;  // average speed of motors is low pass filtered

  smoothDriving();
  float driveTheta = drivePIDcontrol(targetDriveSpeed);

  updateFilteredProx();

  float accelTheta = getAccelTheta(); // reading from accelerometer representing angle
  float gyroOmega = getGyroOmega(); // reading from gyroscope representing angular velocity

  kalmanFilter(accelTheta, gyroOmega);  // updates theta using Kalman filter
  //theta = compFilter(accelTheta, gyroOmega);  // updates theta using complimentary filter

  updateBalanceTheta(tiltDegrees, swivelDegrees);
  float targetTheta = balanceTheta + driveTheta;
  float targetSpeed = balancePIDcontrol(targetTheta);

  driveMotors(targetSpeed);

  setNeck(tiltDegrees, swivelDegrees);

  flexMotors(0, 0, 0, 0, 0, 0, 0, 0);
  
  float currentL = getDriveCurrent(motorLcurrentPin);
  float currentR = getDriveCurrent(motorRcurrentPin);

  float current0 = getFlexCurrent(flex0num);
  float current1 = getFlexCurrent(flex1num);
  float current2 = getFlexCurrent(flex2num);
  float current3 = getFlexCurrent(flex3num);
  float current4 = getFlexCurrent(flex4num);
  float current5 = getFlexCurrent(flex5num);
  float current6 = getFlexCurrent(flex6num);
  float current7 = getFlexCurrent(flex7num);

  serial3Write(theta, proxFL, proxFR, proxBL, proxBR);

  errorCheck();

  // Serial monitoring
  /*Serial.print(dt);
  Serial.write('\t');
  Serial.print(targetDriveSpeed*RPS_TO_MPS);
  Serial.write('\t');
  Serial.print(turnSpeed*RPS_TO_MPS);
  Serial.write('\t');
  Serial.print(tiltDegrees);
  Serial.write('\t');
  Serial.print(swivelDegrees);
  Serial.write('\n');*/
}

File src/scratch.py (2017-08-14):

"""
scratch

Reads control commands wirelessly over bluetooth from a Sony DualShock 3
PlayStation controller. Interprets commands, and converts them into driving
instructions for balancing robot which are written out via serial port to Arduino

Luke Arend
July 2015
Bethel University NanoLab
"""


######## Includes ########
import pygame
import time
import serial
import subprocess
import picamera
import datetime
import sys
import os



######## Global Variable Declarations ########
#### Controller state flag dictionaries ####
buttonValue = {'select': 0,
               'start': 0,
               'clickL': 0,
               'clickR': 0,
               'dPadUp': 0,
               'dPadRight': 0,
               'dPadDown': 0,
               'dPadLeft': 0,
               'triggerL': 0,
               'triggerR': 0,
               'bumperL': 0,
               'bumperR': 0,
               'triangle': 0,
               'circle': 0,
               'cross': 0,
               'square': 0,
               'sum': 0}

axisValue = {'xAxisL': 0,
             'yAxisL': 0,
             'xAxisR': 0,
             'yAxisR': 0,
             'clickL': 0,
             'clickR': 0,
             'dPadUp': 0,
             'dPadRight': 0,
             'dPadDown': 0,
             'dPadLeft': 0,
             'triggerL': 0,
             'triggerR': 0,
             'bumperL': 0,
             'bumperR': 0,
             'triangle': 0,
             'circle': 0,
             'cross': 0,
             'square': 0}

lastButtonValue = {'dPadUp': 0,
                   'dPadRight': 0,
                   'dPadDown': 0,
                   'dPadLeft': 0,
                   'bumperL': 0,
                   'bumperR': 0,
                   'start': 0,
                   'triangle': 0,
                   'circle': 0,
                   'cross': 0,
                   'square': 0,
                   'sum': 0}

controllerOptions = {'mapping': True, #True is turn/drive, False is left/right
                     'invertMult': 1,
                     'powerMult': .5,
                     'smoothing': 1,
                     'autonomous': False,
                     'previewing': False}



######## Initialization ########
print("Launching initialization...")
print()
#### Initialize pygame ####
print("Initializing pygame...")
pygame.init()
print()


#### Initialize controller ####
print("Initializing controller connection...")
joystickAvailable = pygame.joystick.get_count() # check if joystick is available
while(joystickAvailable == 0): # if not, try re-launching sixad
  print("Controller connection failed.")
  time.sleep(1)
  print("Configuring DualShock 3 controller...")
  time.sleep(1)
  sixad = subprocess.Popen(["/usr/bin/sixad", "--stop"],
                                     universal_newlines=True)
  sixad = subprocess.Popen(["/usr/bin/sixad", "--start"],
                           universal_newlines=True)
  timeout = 10  # timeout for connection loop in seconds
  startTime = time.time()
  print("Trying to connect (please press PS3 button)...")
  while(time.time() - startTime < timeout):
    pygame.joystick.quit()
    pygame.joystick.init()
    joystickAvailable = pygame.joystick.get_count()
    if(joystickAvailable != 0):
      break
  if(joystickAvailable != 0):
      break
  else:
    print("Connection process timed out.")
    time.sleep(1)
print("Controller found!")
print()
  
print("Initializing controller instance...")
dualshock = pygame.joystick.Joystick(0) # create joystick instance for DualShock
dualshock.init()

print("Initialized joystick: '%s'" % dualshock.get_name())    # print some useful info
print("Number of axes: %s" % dualshock.get_numaxes())
print("Number of trackballs: %s" % dualshock.get_numballs())
print("Number of buttons: %s" % dualshock.get_numbuttons())
print("Number of hats: %s" % dualshock.get_numhats())
print()


#### Initialize serial port ####
def initializeSerial(portName): # recursive function to attempt to open serial port
  try:
    port = serial.Serial(portName, baudrate=115200, timeout=.005)
  except OSError:
    print("Port '%s' not found." % portName)
    time.sleep(5)
    """print("Please check cable connection, then press 'start' to try again.")
    while(True):
      events = pygame.event.get()   
      for event in events:
        if(event.type == 10 and event.button == 3):
          break
      else:
        continue # if for loop not broken, continue
      break"""
    print("Re-attempting to initialize serial port '%s'..." % portName)
    port = initializeSerial(portName)
  return port

portName = '/dev/ttyAMA0'
#portName = '/dev/ttyACM0'
print("Initializing serial port '%s'..." % portName)
"""print("Press 'start' to open serial connection.")
while(True):
  events = pygame.event.get()   
  for event in events:
    if(event.type == 10 and event.button == 3):
      break
  else:
    continue # if for loop not broken, continue
  break"""
port = initializeSerial(portName)
port.flushInput()
port.flushOutput()
#time.sleep(1)
print("Serial port '%s' opened successfully." % portName)
print()


#### Initialize PiCamera ####
print("Initializing camera...")
try:
  camera = picamera.PiCamera()
  camera.resolution = (1024, 768)
except picamera.exc.PiCameraError:
  print("Camera is not enabled.")
print()

print("Initialization complete!")
print()
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
